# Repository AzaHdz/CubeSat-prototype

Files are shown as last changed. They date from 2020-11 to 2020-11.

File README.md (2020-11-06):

# CubeSat-prototype
Design, Build and test
###### STR: Structure, EPS: Electrical power Subsystem, CDH: Command data and handling, COM: Communications, ADC: Attitude Determination and Control, GCS: Ground Control Station
#### The purpose of this project is to develop the prototype of a CubeSat 1U type satellite, used in real space missions. 
#### 6 subsystems and a Ground control station were designed: EPS, Payload, CDH, COM, ADC, GCS and STR.
#### each subsystem was designed, built and tested
#### Communication protocols used: UART, I2C, Analog, SPI, Zigbee
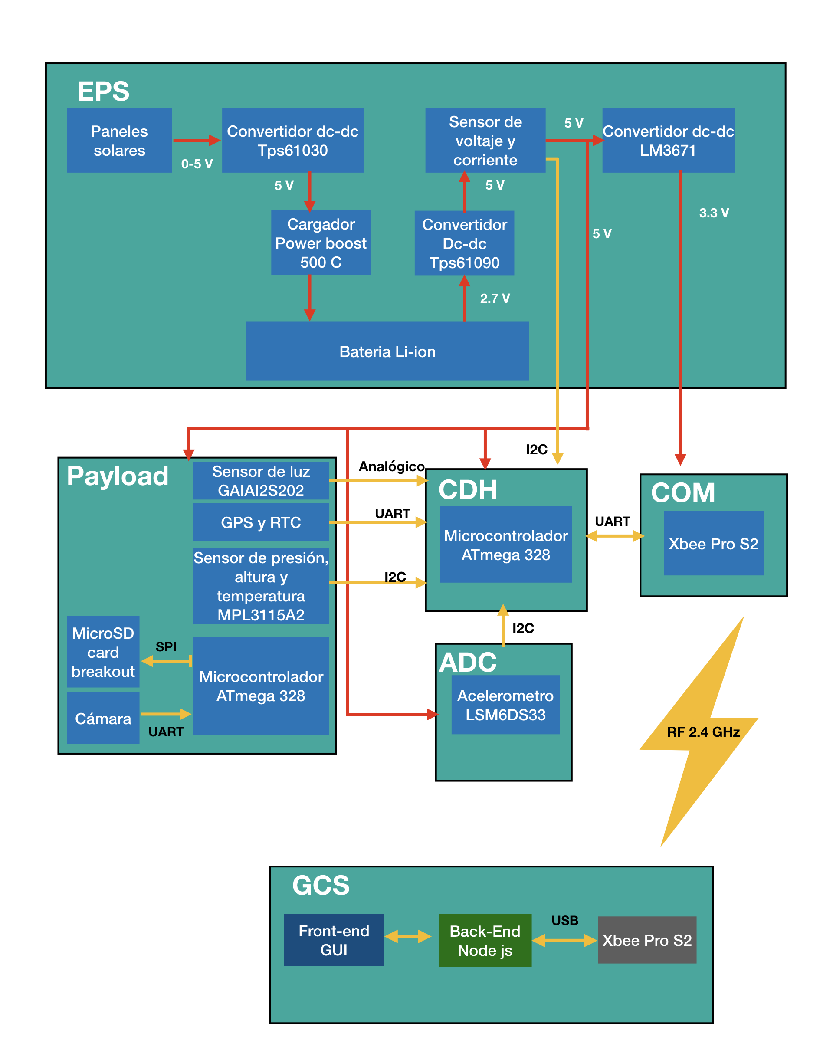
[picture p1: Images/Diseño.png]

#### The STR was designed in fusion 360 and built with  a 3d printer.
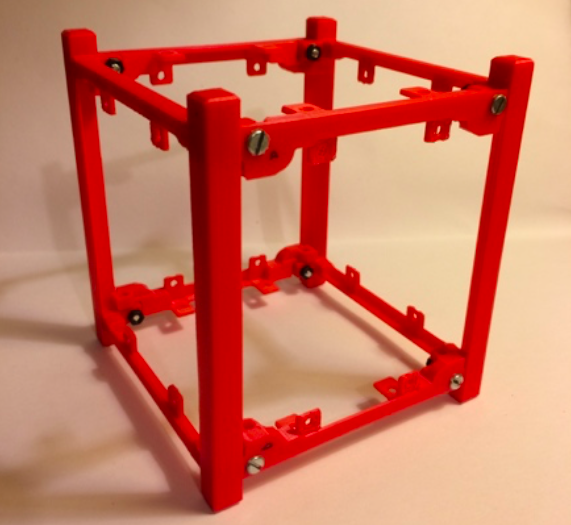
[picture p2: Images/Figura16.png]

#### 5 pcb were designed in eagle and later they were manufactured in a chinese company
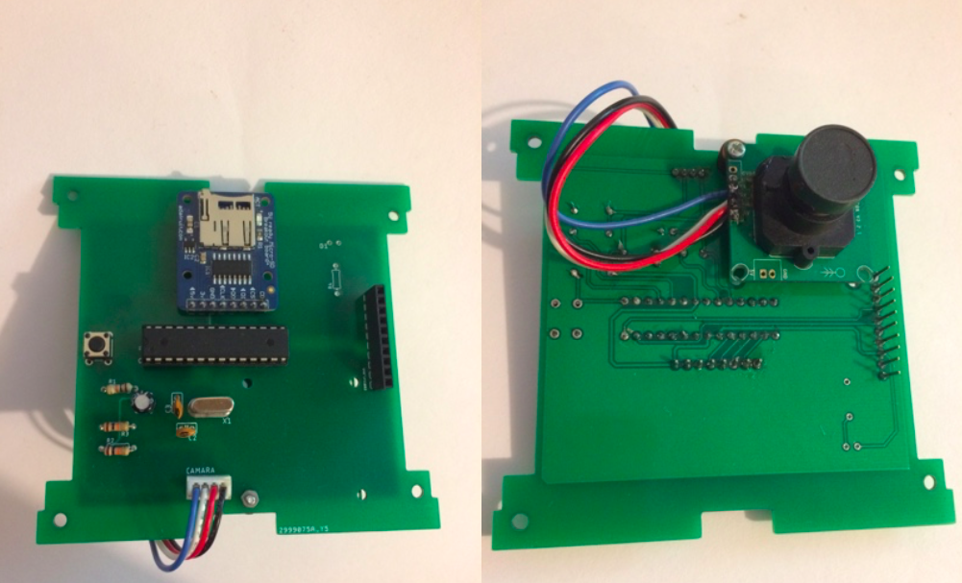
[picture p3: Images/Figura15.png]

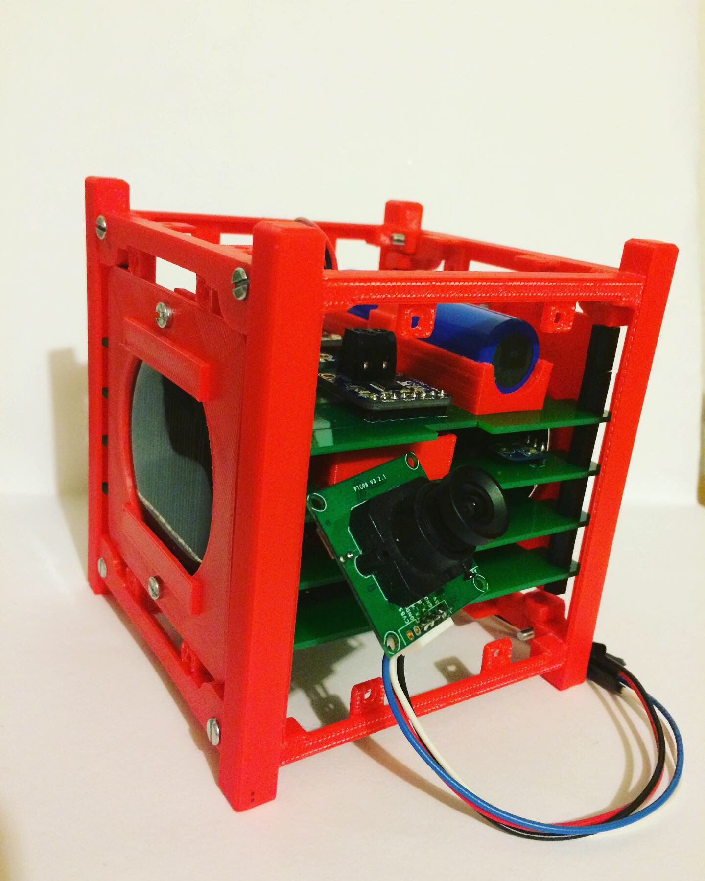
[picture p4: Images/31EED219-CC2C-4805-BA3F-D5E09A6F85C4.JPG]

#### The two microcontrollers were programmed with the Arduino IDE.
#### The GUI was built with Node js and deployed as a web App.
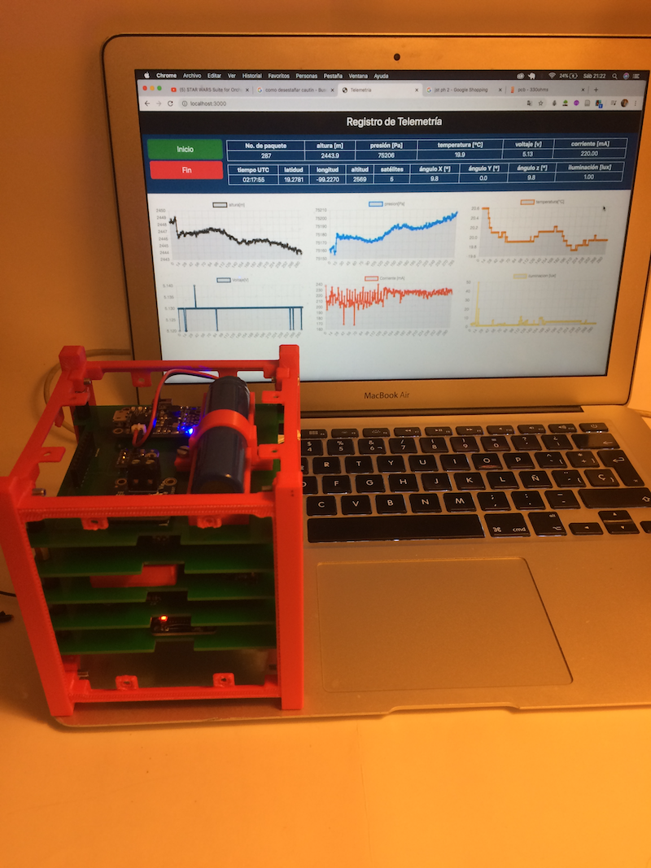
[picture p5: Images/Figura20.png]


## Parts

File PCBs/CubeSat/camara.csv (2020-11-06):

Part | Value | Device | Package | Description | POPULARITY | PROD_ID | SF_SKU | SPICEPREFIX | VALUE
C1 | 10 uF | C-US025-025X050 | C025-025X050 | CAPACITOR, American symbol | 0 |  |  | C
C2 | 22 pF | C-US025-025X050 | C025-025X050 | CAPACITOR, American symbol | 0 |  |  | C
C3 | 22 | C-US025-025X050 | C025-025X050 | CAPACITOR, American symbol | 0 |  |  | C
CAMARA |  | JST-PH4 | JST-PH4
CUBESAT_BUS |  | CONN_10";1X10" | Multi connection point. Often used as Generic Header-pin footprint for 0.1 inch spaced/style header connections |  | CONN-11563
D1 |  | BEAGLEBONE_BLUE_LED-3MM-NO_SILK | BEAGLEBONE_BLUE_BEAGLEBONE_BLUE_LED3MM-NS | LEDs
MEMORIASD |  | CONN_08";1X08" | Multi connection point. Often used as Generic Header-pin footprint for 0.1 inch spaced/style header connections |  | CONN-08438
R1 |  | R-US_0204/7 | 0204/7 | RESISTOR, American symbol | 48 |  |  | 10k
R2 | 10 k | R-US_0204/7 | 0204/7 | RESISTOR, American symbol | 48 |  |  | R
R3 | 10 k | R-US_0204/7 | 0204/7 | RESISTOR, American symbol | 48 |  |  | R
R4 | 330 | R-US_0204/7 | 0204/7 | RESISTOR, American symbol | 48 |  |  | R
S1 | MOMENTARY-SWITCH-SPST-PTH-6.0MM | MOMENTARY-SWITCH-SPST-PTH-6.0MM | TACTILE_SWITCH_PTH_6.0MM | Momentary Switch (Pushbutton) - SPST |  | SWCH-08441 | COM-00097
U1 | 328P | ATMEGA328P_PDIP | DIP28 | Atmel 328P |  | IC-09136 |  |  | 328P
X1 | CRYSTALS-NOGND-HC49 | CRYSTALS-NOGND-HC49 | HC49 | CRYSTALS CAN NOT GROUNDED | 16MHZ

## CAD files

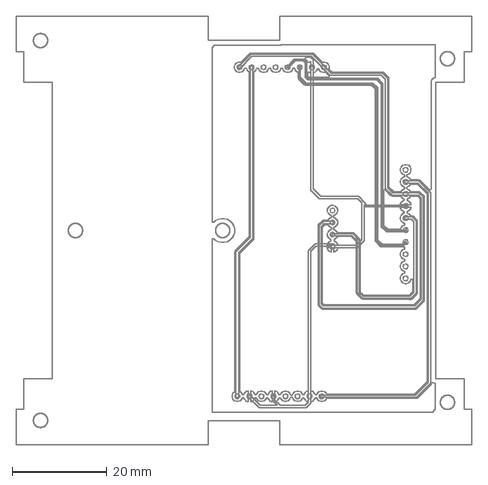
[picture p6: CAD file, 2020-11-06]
PCBs/CubeSat/bateria EPS.dxf
95.9 x 90.2 mm

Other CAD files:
Structure/STR.f3z

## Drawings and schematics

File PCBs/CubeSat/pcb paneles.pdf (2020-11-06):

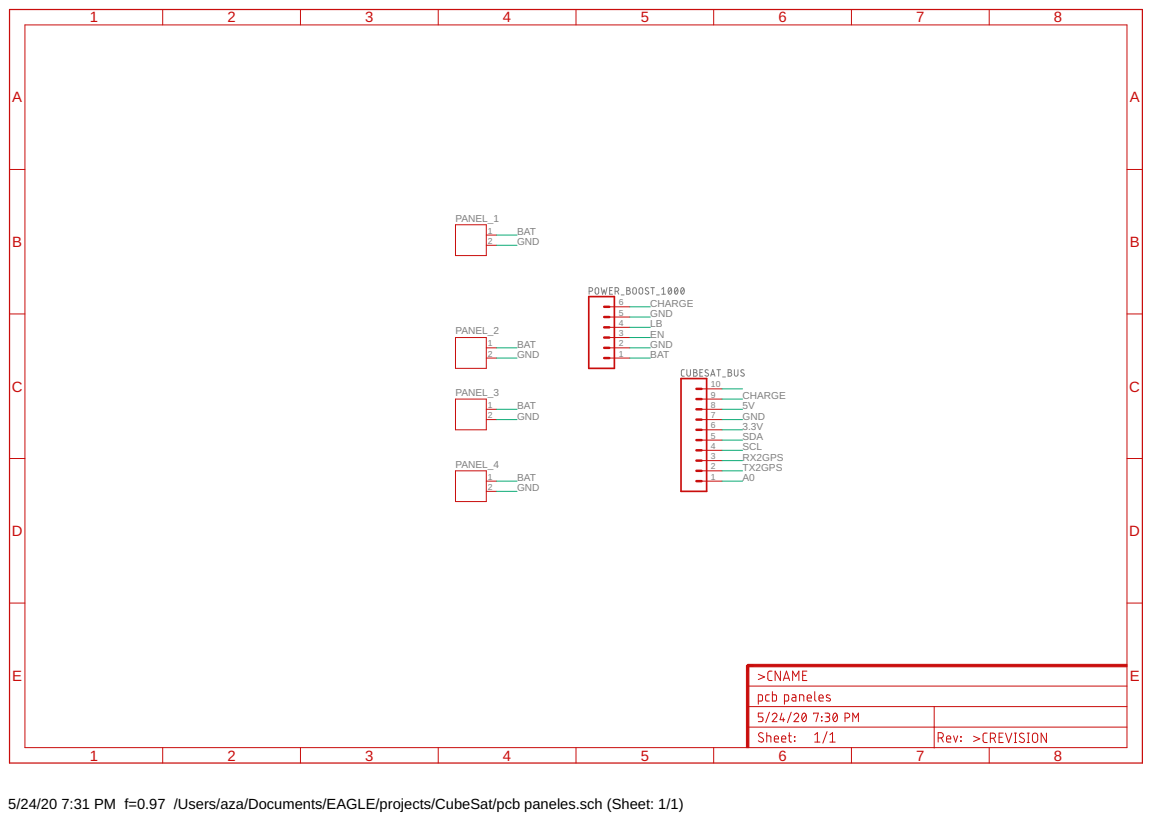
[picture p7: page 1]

5/24/20 7:31 PM f=0.97 /Users/aza/Documents/EAGLE/projects/CubeSat/pcb paneles.sch (Sheet: 1/1)

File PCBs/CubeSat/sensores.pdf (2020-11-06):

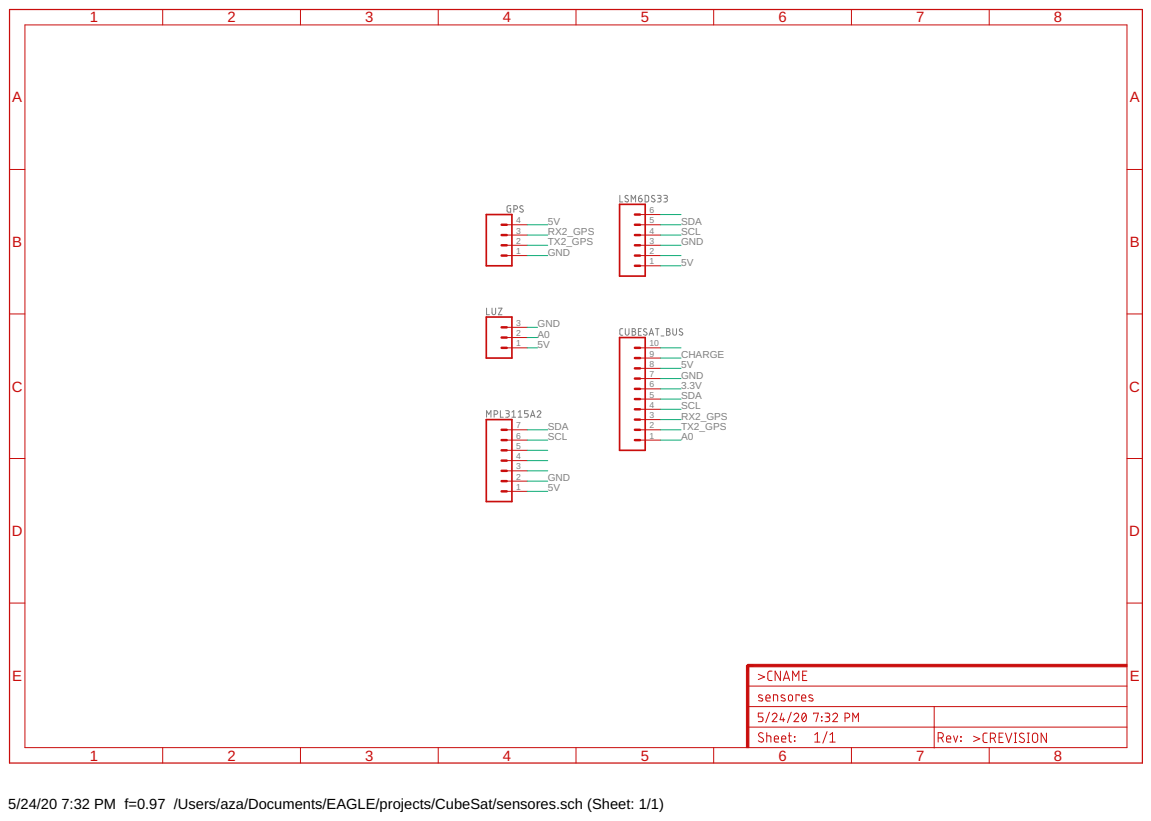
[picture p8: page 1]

5/24/20 7:32 PM f=0.97 /Users/aza/Documents/EAGLE/projects/CubeSat/sensores.sch (Sheet: 1/1)

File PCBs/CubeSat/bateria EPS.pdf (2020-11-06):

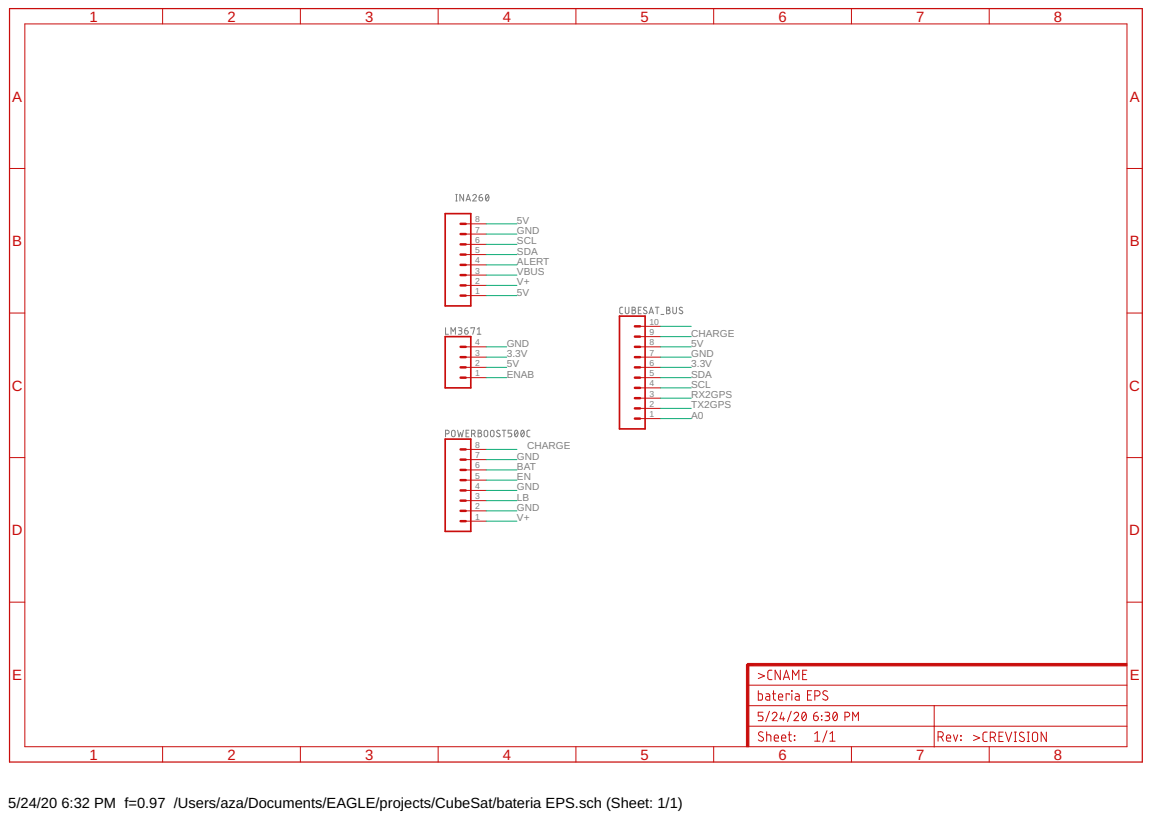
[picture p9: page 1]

5/24/20 6:32 PM f=0.97 /Users/aza/Documents/EAGLE/projects/CubeSat/bateria EPS.sch (Sheet: 1/1)

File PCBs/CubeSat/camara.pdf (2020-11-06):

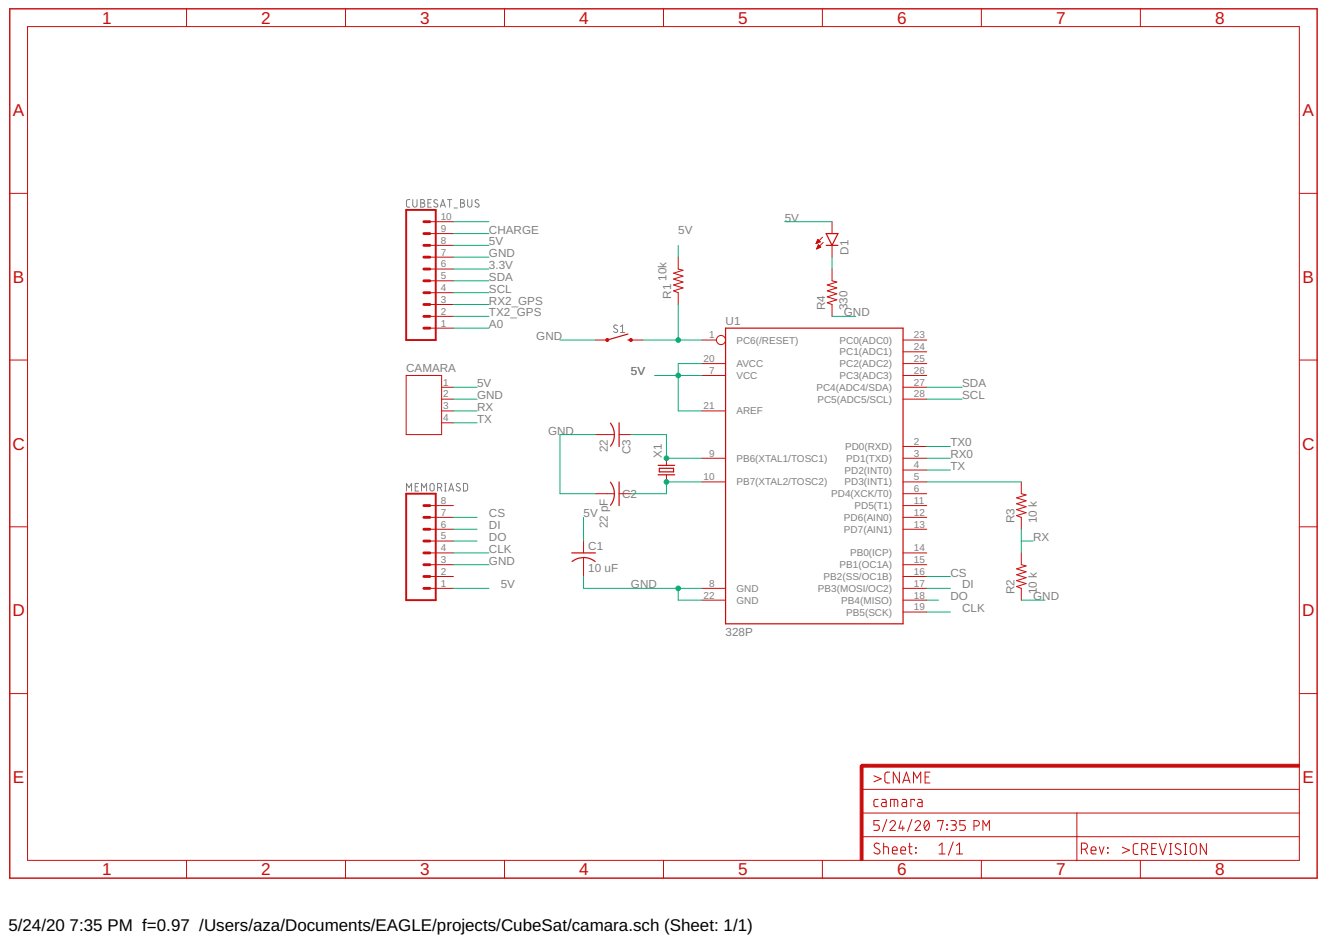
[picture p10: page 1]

5/24/20 7:35 PM f=0.97 /Users/aza/Documents/EAGLE/projects/CubeSat/camara.sch (Sheet: 1/1)

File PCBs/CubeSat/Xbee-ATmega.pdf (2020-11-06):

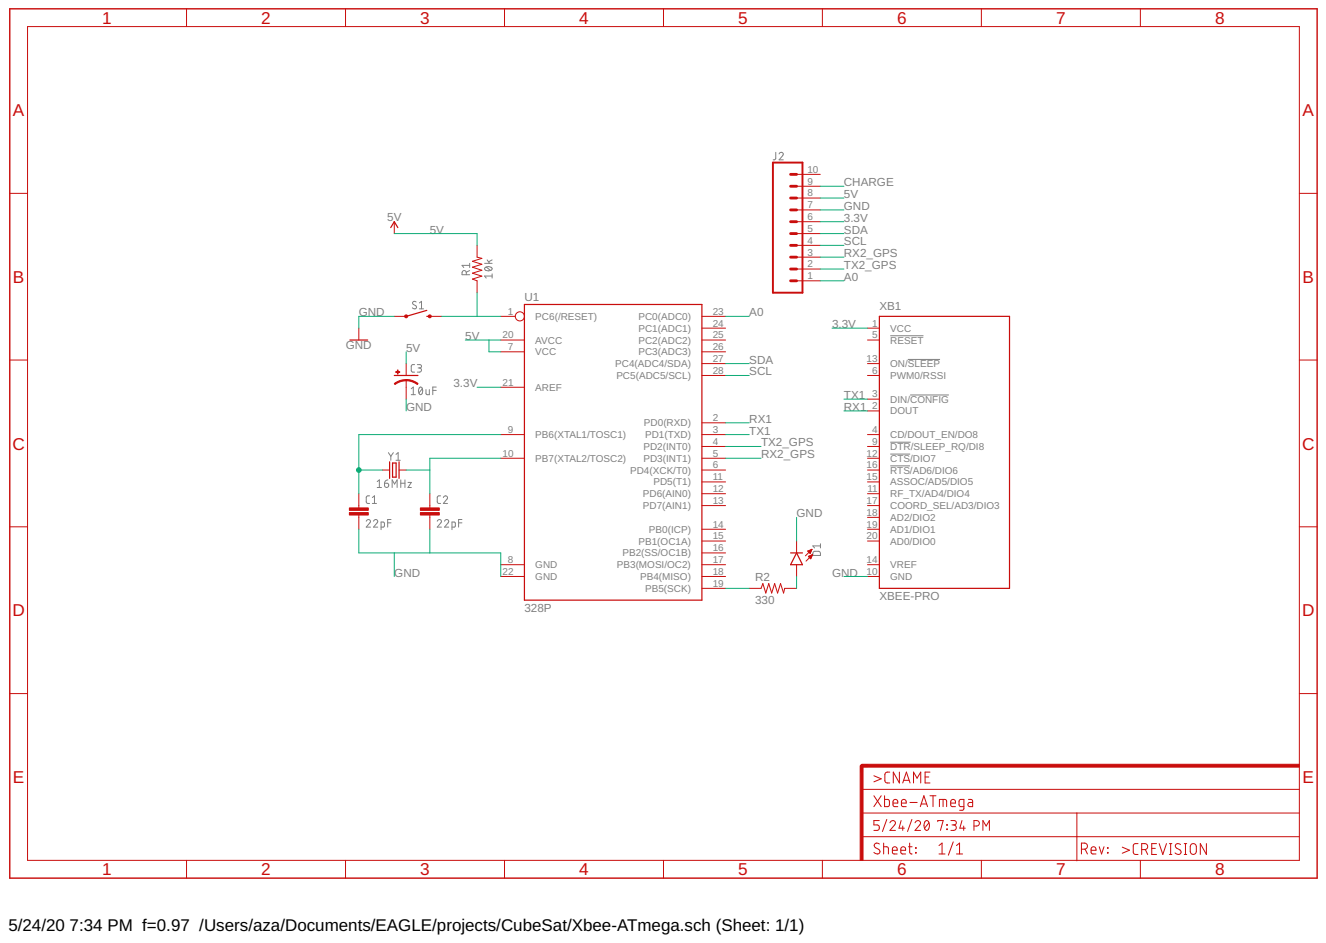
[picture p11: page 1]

5/24/20 7:34 PM f=0.97 /Users/aza/Documents/EAGLE/projects/CubeSat/Xbee-ATmega.sch (Sheet: 1/1)

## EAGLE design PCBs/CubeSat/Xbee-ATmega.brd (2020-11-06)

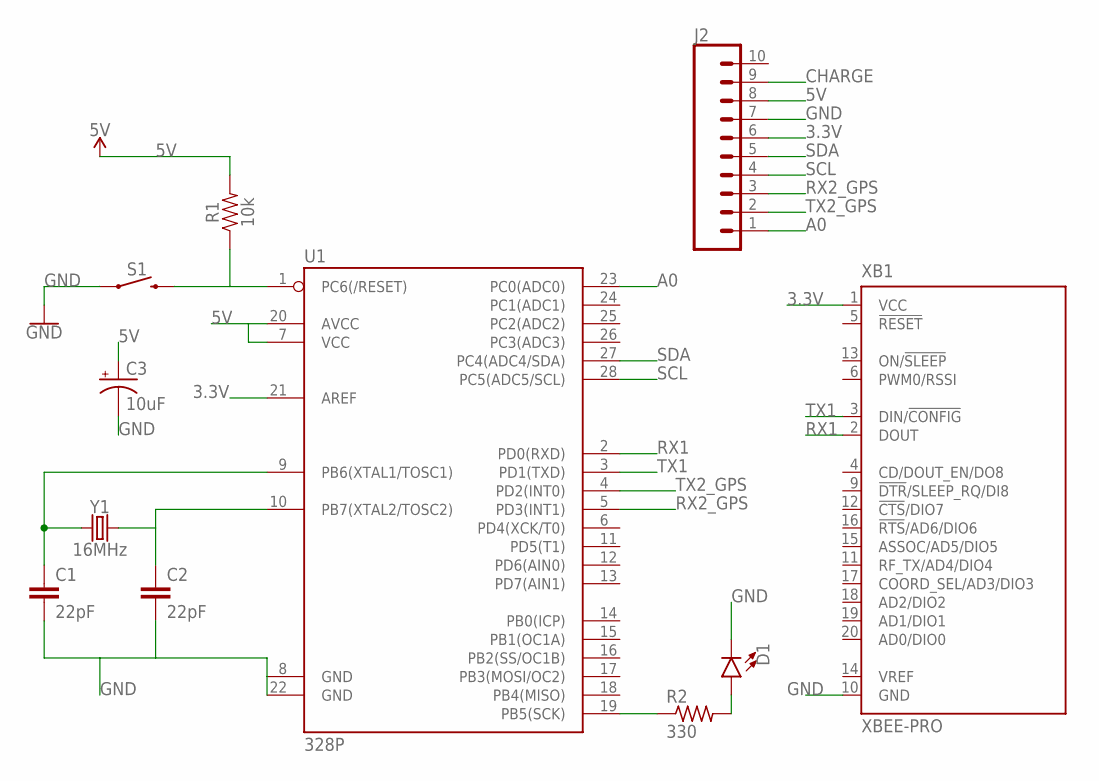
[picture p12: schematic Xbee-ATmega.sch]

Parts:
C1, C2: 22pF; CAP-PTH-2.54
C3: 10uF; CPOL-RADIAL-2.5MM-5MM
D1: LED5MM; LED_5MM
J2: CONN_10"; 1X10
R1: 10k; AXIAL-0.3
R2: 330; 0207/7
S1: MOMENTARY-SWITCH-SPST-PTH-6.0MM; TACTILE_SWITCH_PTH_6.0MM
U1: 328P; DIP28
XB1: XBEE-PRO
Y1: 16MHz; HC49US

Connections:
3.3V: J2.6, U1.21 (AREF), XB1.1 (VCC)
5V: C3.1 (+), J2.8, R1.P$2 (2), U1.7 (VCC), U1.20 (AVCC)
A0: J2.1, U1.23 (PC0(ADC0))
CHARGE: J2.9
GND: C1.2, C2.2, C3.2 (-), D1.K (C), J2.7, S1.1, U1.8 (GND), U1.22 (GND), XB1.10 (GND)
unnamed: R1.P$1 (1), S1.3 (2), U1.1 (PC6(/RESET))
unnamed: C2.1, U1.10 (PB7(XTAL2/TOSC2)), Y1.2
unnamed: C1.1, U1.9 (PB6(XTAL1/TOSC1)), Y1.1
unnamed: R2.1, U1.19 (PB5(SCK))
unnamed: D1.A, R2.2
RX1: U1.2 (PD0(RXD)), XB1.2 (DOUT)
RX2_GPS: J2.3, U1.5 (PD3(INT1))
SCL: J2.4, U1.28 (PC5(ADC5/SCL))
SDA: J2.5, U1.27 (PC4(ADC4/SDA))
TX1: U1.3 (PD1(TXD)), XB1.3 (DIN/!CONFIG)
TX2_GPS: J2.2, U1.4 (PD2(INT0))

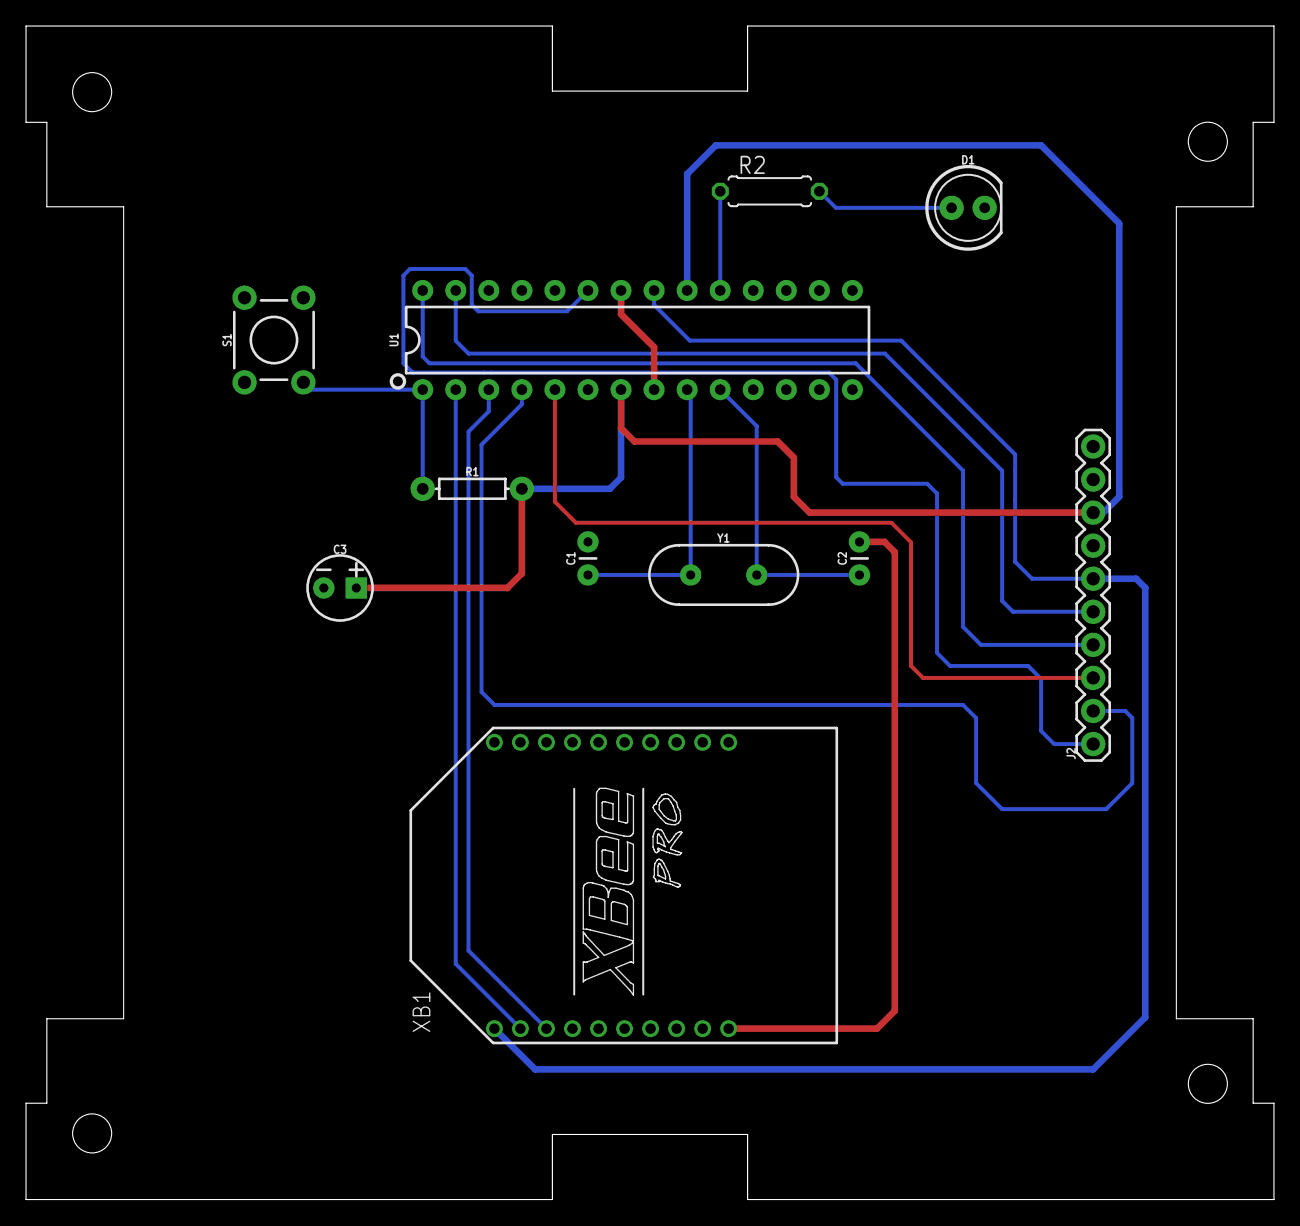
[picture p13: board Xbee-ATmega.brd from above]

Board: 2 copper layers, 95.9 x 90.2 mm, 11 parts (0 on the bottom side), 15 nets.

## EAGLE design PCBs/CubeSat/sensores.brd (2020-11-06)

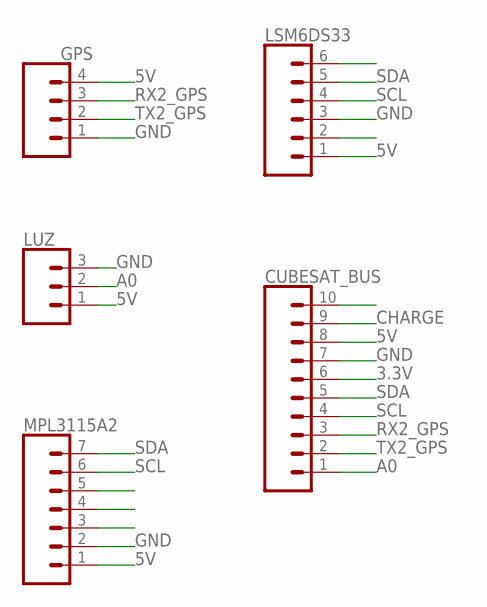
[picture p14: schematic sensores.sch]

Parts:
CUBESAT_BUS: CONN_10"; 1X10
GPS: CONN_04; 1X04
LSM6DS33: CONN_06SILK_FEMALE_PTH; 1X06
LUZ: CONN_03; 1X03
MPL3115A2: CONN_07; 1X07

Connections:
3.3V: CUBESAT_BUS.6
5V: CUBESAT_BUS.8, GPS.4, LSM6DS33.1, LUZ.1, MPL3115A2.1
A0: CUBESAT_BUS.1, LUZ.2
CHARGE: CUBESAT_BUS.9
GND: CUBESAT_BUS.7, GPS.1, LSM6DS33.3, LUZ.3, MPL3115A2.2
RX2_GPS: CUBESAT_BUS.3, GPS.3
SCL: CUBESAT_BUS.4, LSM6DS33.4, MPL3115A2.6
SDA: CUBESAT_BUS.5, LSM6DS33.5, MPL3115A2.7
TX2_GPS: CUBESAT_BUS.2, GPS.2

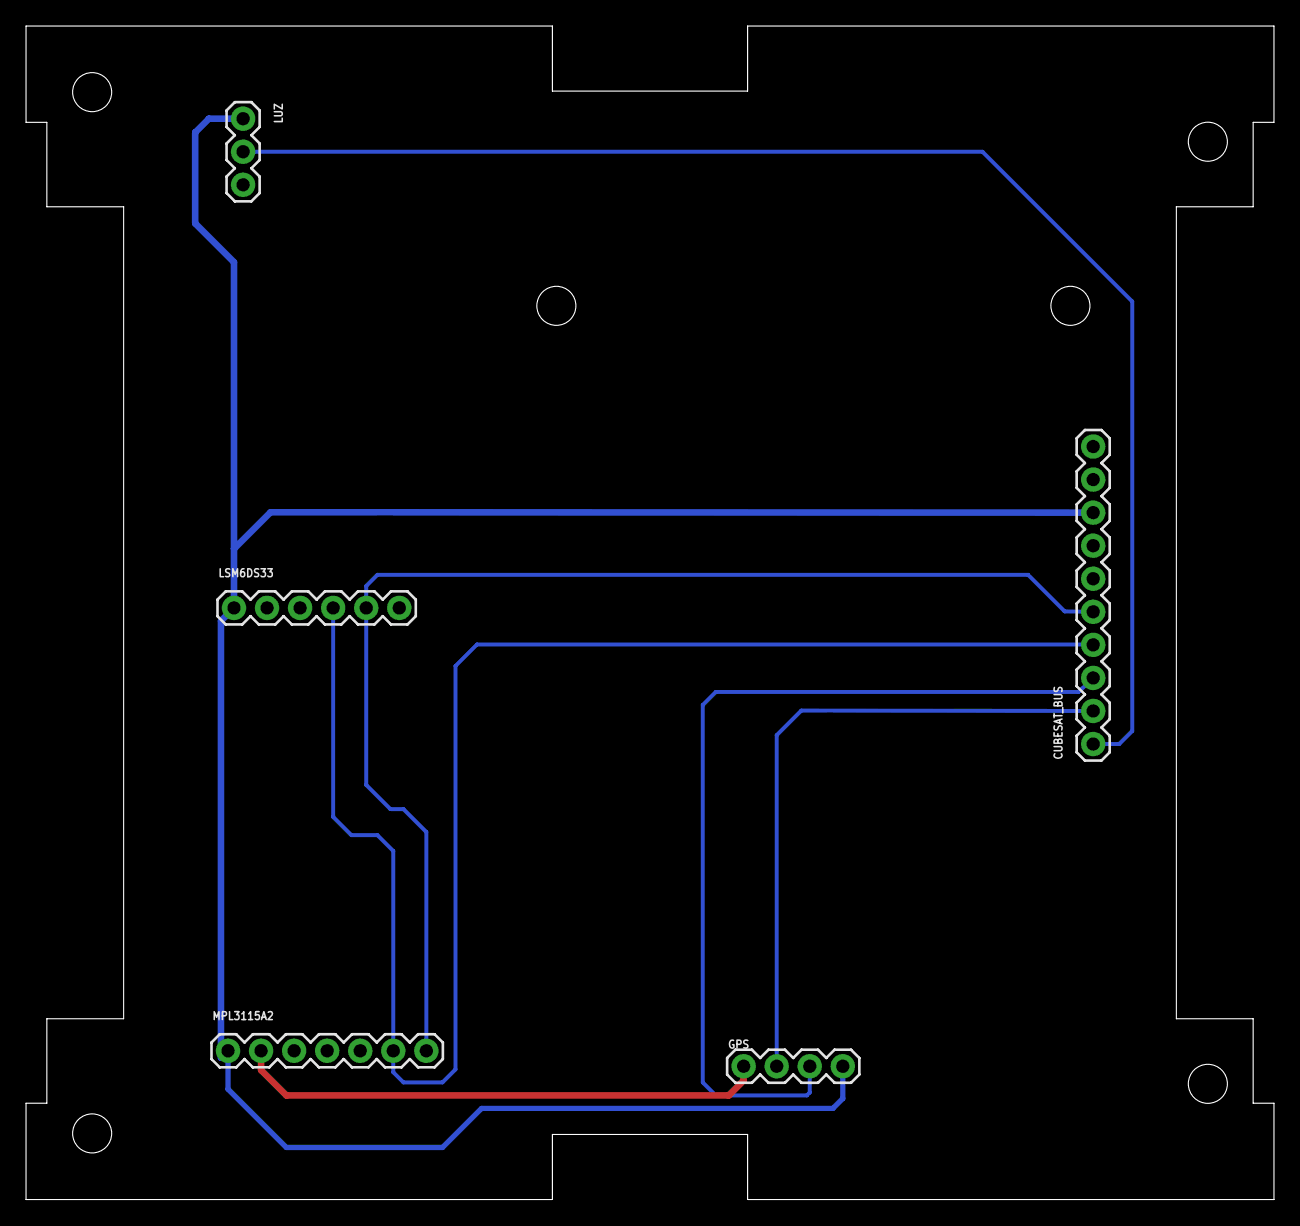
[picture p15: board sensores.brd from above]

Board: 2 copper layers, 95.9 x 90.2 mm, 5 parts (0 on the bottom side), 7 nets.

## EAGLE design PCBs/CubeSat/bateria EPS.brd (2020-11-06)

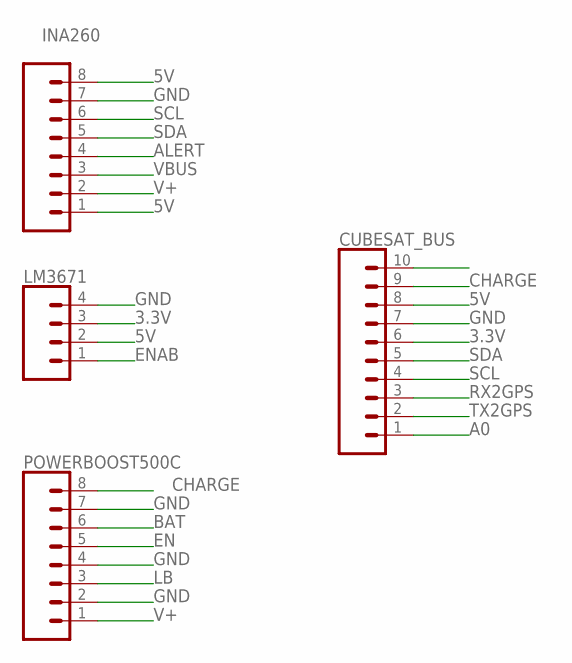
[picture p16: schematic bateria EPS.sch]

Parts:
CUBESAT_BUS: CONN_10"; 1X10
INA260: CONN_08"; 1X08
LM3671: CONN_04PTH; 1X04
POWERBOOST500C: CONN_08"; 1X08

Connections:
3.3V: CUBESAT_BUS.6, LM3671.3
5V: CUBESAT_BUS.8, INA260.1, INA260.8, LM3671.2
A0: CUBESAT_BUS.1
ALERT: INA260.4
BAT: POWERBOOST500C.6
CHARGE: CUBESAT_BUS.9, POWERBOOST500C.8
EN: POWERBOOST500C.5
ENAB: LM3671.1
GND: CUBESAT_BUS.7, INA260.7, LM3671.4, POWERBOOST500C.2, POWERBOOST500C.4, POWERBOOST500C.7
LB: POWERBOOST500C.3
RX2GPS: CUBESAT_BUS.3
SCL: CUBESAT_BUS.4, INA260.6
SDA: CUBESAT_BUS.5, INA260.5
TX2GPS: CUBESAT_BUS.2
V+: INA260.2, POWERBOOST500C.1
VBUS: INA260.3

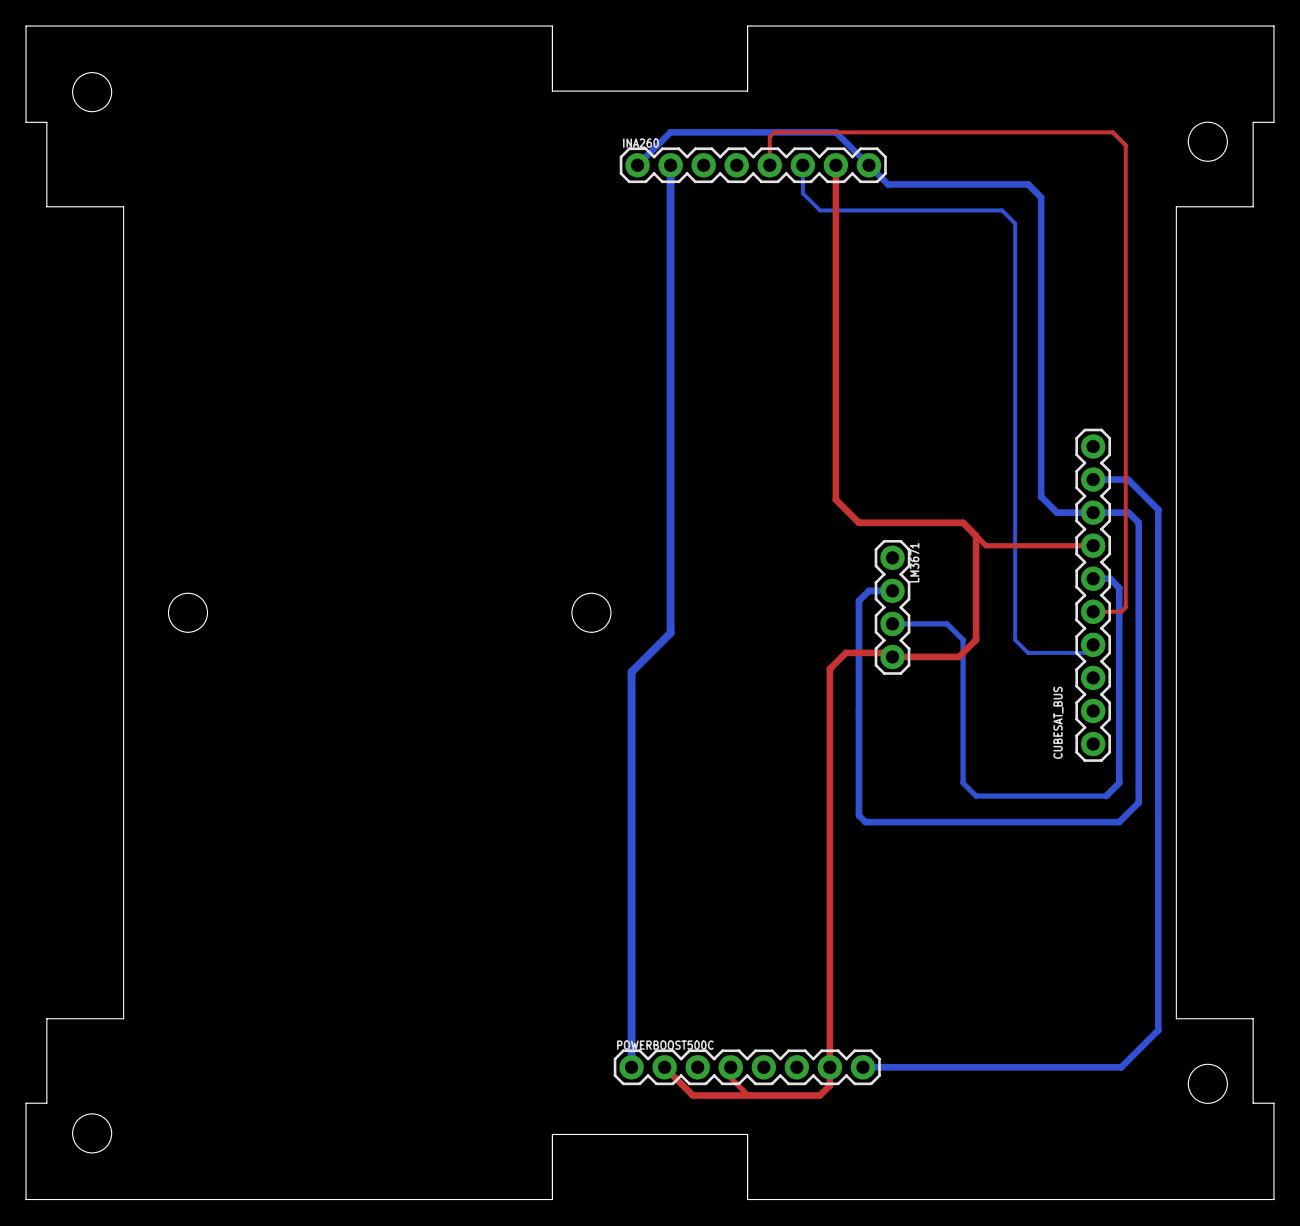
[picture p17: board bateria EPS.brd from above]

Board: 2 copper layers, 95.9 x 90.2 mm, 4 parts (0 on the bottom side), 7 nets.

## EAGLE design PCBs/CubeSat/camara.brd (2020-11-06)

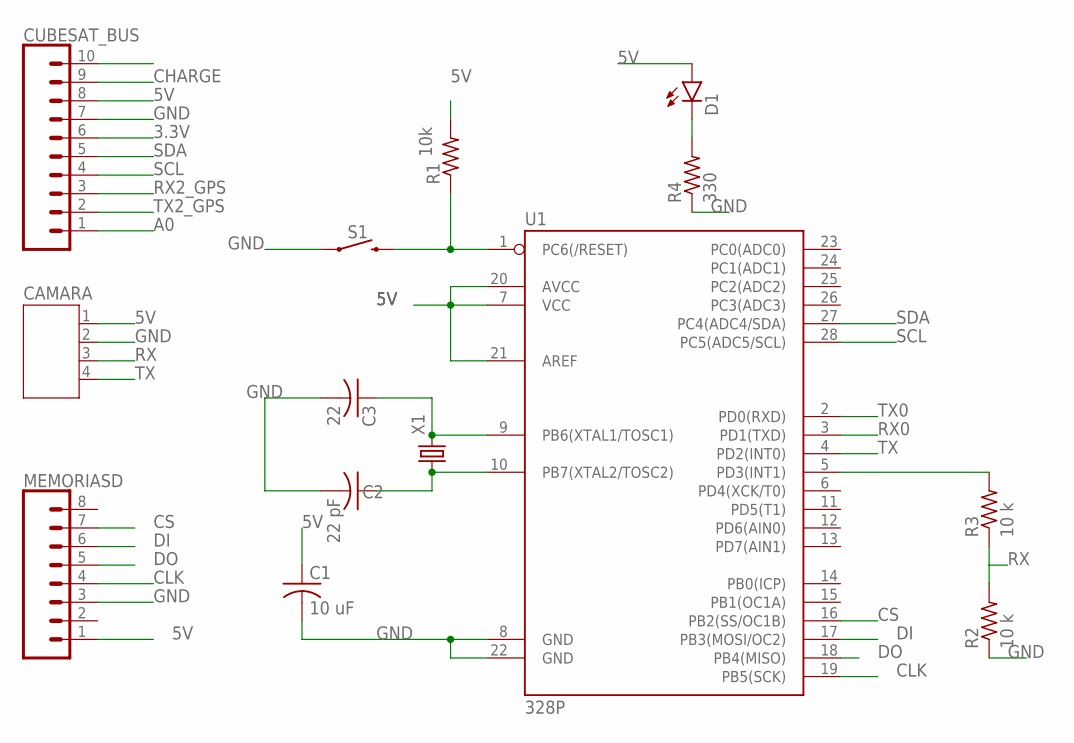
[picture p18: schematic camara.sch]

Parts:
C1: 10 uF; C025-025X050
C2: 22 pF; C025-025X050
C3: 22; C025-025X050
CAMARA: JST-PH4
CUBESAT_BUS: CONN_10"; 1X10
D1: BEAGLEBONE_BLUE_LED-3MM-NO_SILK; BEAGLEBONE_BLUE_BEAGLEBONE_BLUE_LED3MM-NS
MEMORIASD: CONN_08"; 1X08
R1: R-US_0204/7; 0204/7
R2, R3: 10 k; 0204/7
R4: 330; 0204/7
S1: MOMENTARY-SWITCH-SPST-PTH-6.0MM; TACTILE_SWITCH_PTH_6.0MM
U1: 328P; DIP28
X1: CRYSTALS-NOGND-HC49; HC49

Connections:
3.3V: CUBESAT_BUS.6
5V: C1.1, CAMARA.1, CUBESAT_BUS.8, D1.A, MEMORIASD.1, R1.2, U1.7 (VCC), U1.20 (AVCC), U1.21 (AREF)
A0: CUBESAT_BUS.1
CHARGE: CUBESAT_BUS.9
CLK: MEMORIASD.4, U1.19 (PB5(SCK))
CS: MEMORIASD.7, U1.16 (PB2(SS/OC1B))
DI: MEMORIASD.6, U1.17 (PB3(MOSI/OC2))
DO: MEMORIASD.5, U1.18 (PB4(MISO))
GND: C1.2, C2.2, C3.2, CAMARA.2, CUBESAT_BUS.7, MEMORIASD.3, R2.1, R4.1, S1.1, U1.8 (GND), U1.22 (GND)
unnamed: R1.1, S1.3 (2), U1.1 (PC6(/RESET))
unnamed: C3.1, U1.9 (PB6(XTAL1/TOSC1)), X1.2
unnamed: C2.1, U1.10 (PB7(XTAL2/TOSC2)), X1.1
unnamed: R3.2, U1.5 (PD3(INT1))
unnamed: D1.K (C), R4.2
RX: CAMARA.3, R2.2, R3.1
RX0: U1.3 (PD1(TXD))
RX2_GPS: CUBESAT_BUS.3
SCL: CUBESAT_BUS.4, U1.28 (PC5(ADC5/SCL))
SDA: CUBESAT_BUS.5, U1.27 (PC4(ADC4/SDA))
TX: CAMARA.4, U1.4 (PD2(INT0))
TX0: U1.2 (PD0(RXD))
TX2_GPS: CUBESAT_BUS.2

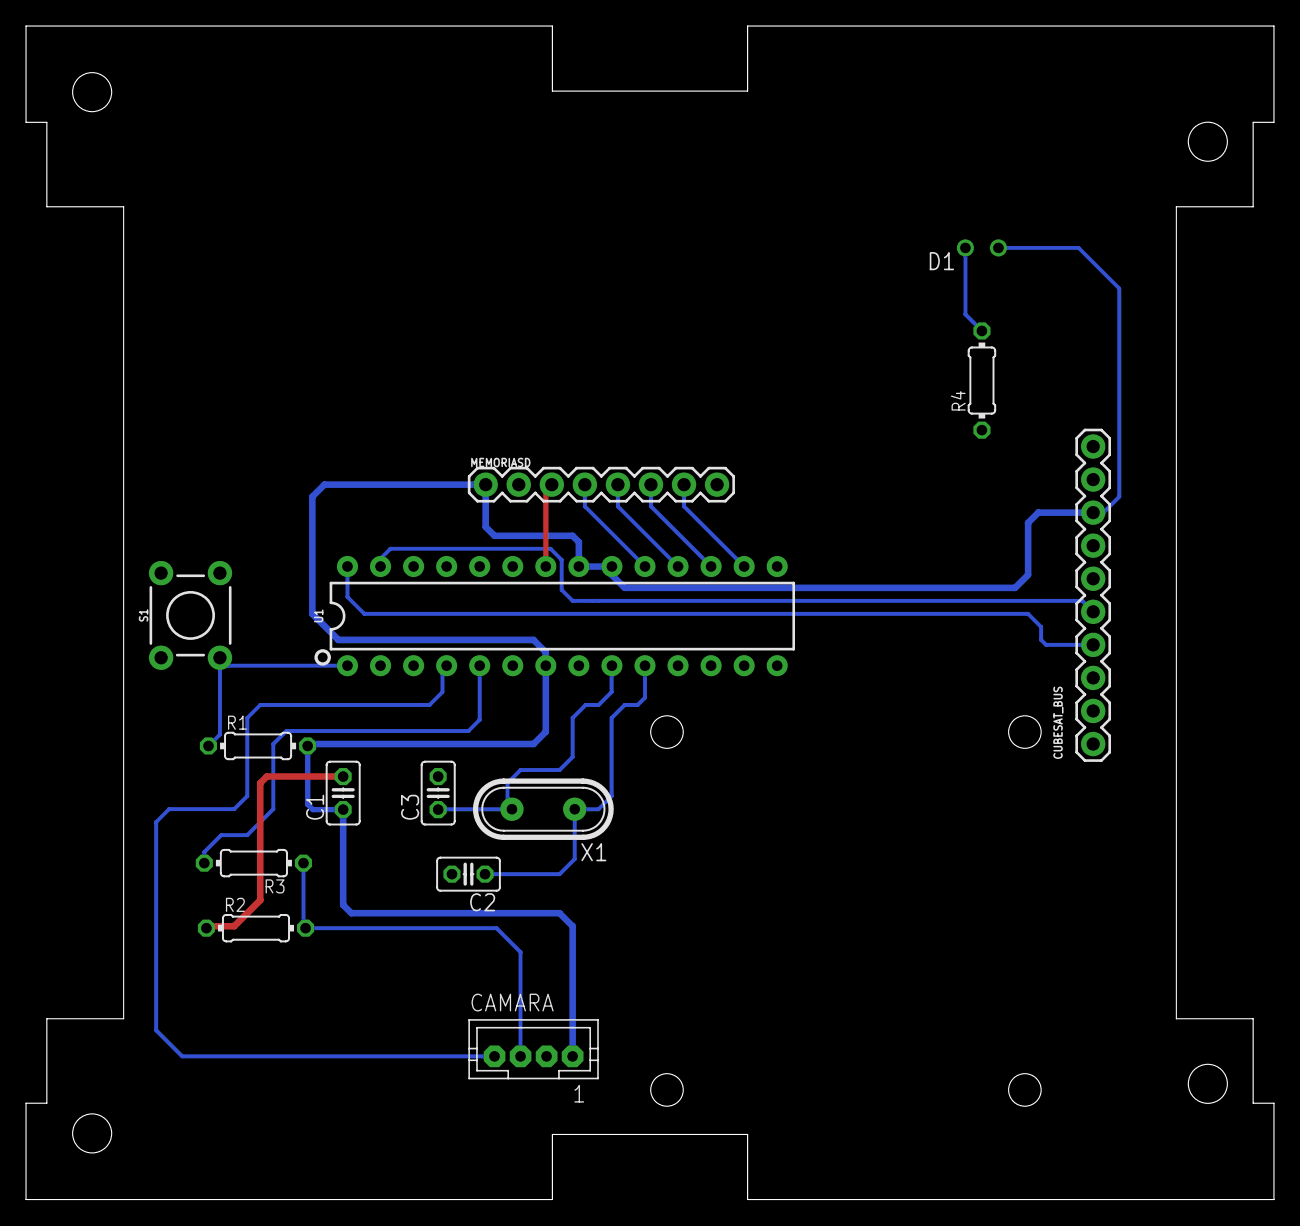
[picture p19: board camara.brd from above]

Board: 2 copper layers, 95.9 x 90.2 mm, 14 parts (0 on the bottom side), 15 nets.

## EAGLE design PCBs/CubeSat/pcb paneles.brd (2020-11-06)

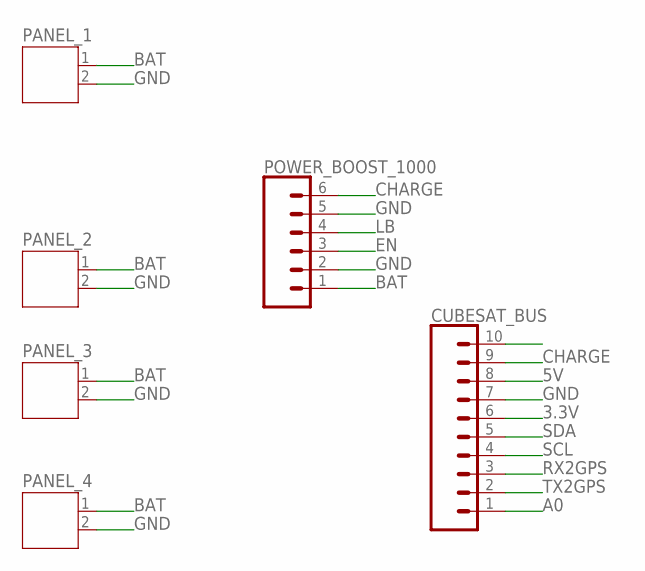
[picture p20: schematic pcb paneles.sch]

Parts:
CUBESAT_BUS: CONN_10"; 1X10
PANEL_1, PANEL_2, PANEL_3, PANEL_4: JST-PH2
POWER_BOOST_1000: CONN_06SILK_FEMALE_PTH; 1X06

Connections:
3.3V: CUBESAT_BUS.6
5V: CUBESAT_BUS.8
A0: CUBESAT_BUS.1
BAT: PANEL_1.1, PANEL_2.1, PANEL_3.1, PANEL_4.1, POWER_BOOST_1000.1
CHARGE: CUBESAT_BUS.9, POWER_BOOST_1000.6
EN: POWER_BOOST_1000.3
GND: CUBESAT_BUS.7, PANEL_1.2, PANEL_2.2, PANEL_3.2, PANEL_4.2, POWER_BOOST_1000.2, POWER_BOOST_1000.5
LB: POWER_BOOST_1000.4
RX2GPS: CUBESAT_BUS.3
SCL: CUBESAT_BUS.4
SDA: CUBESAT_BUS.5
TX2GPS: CUBESAT_BUS.2

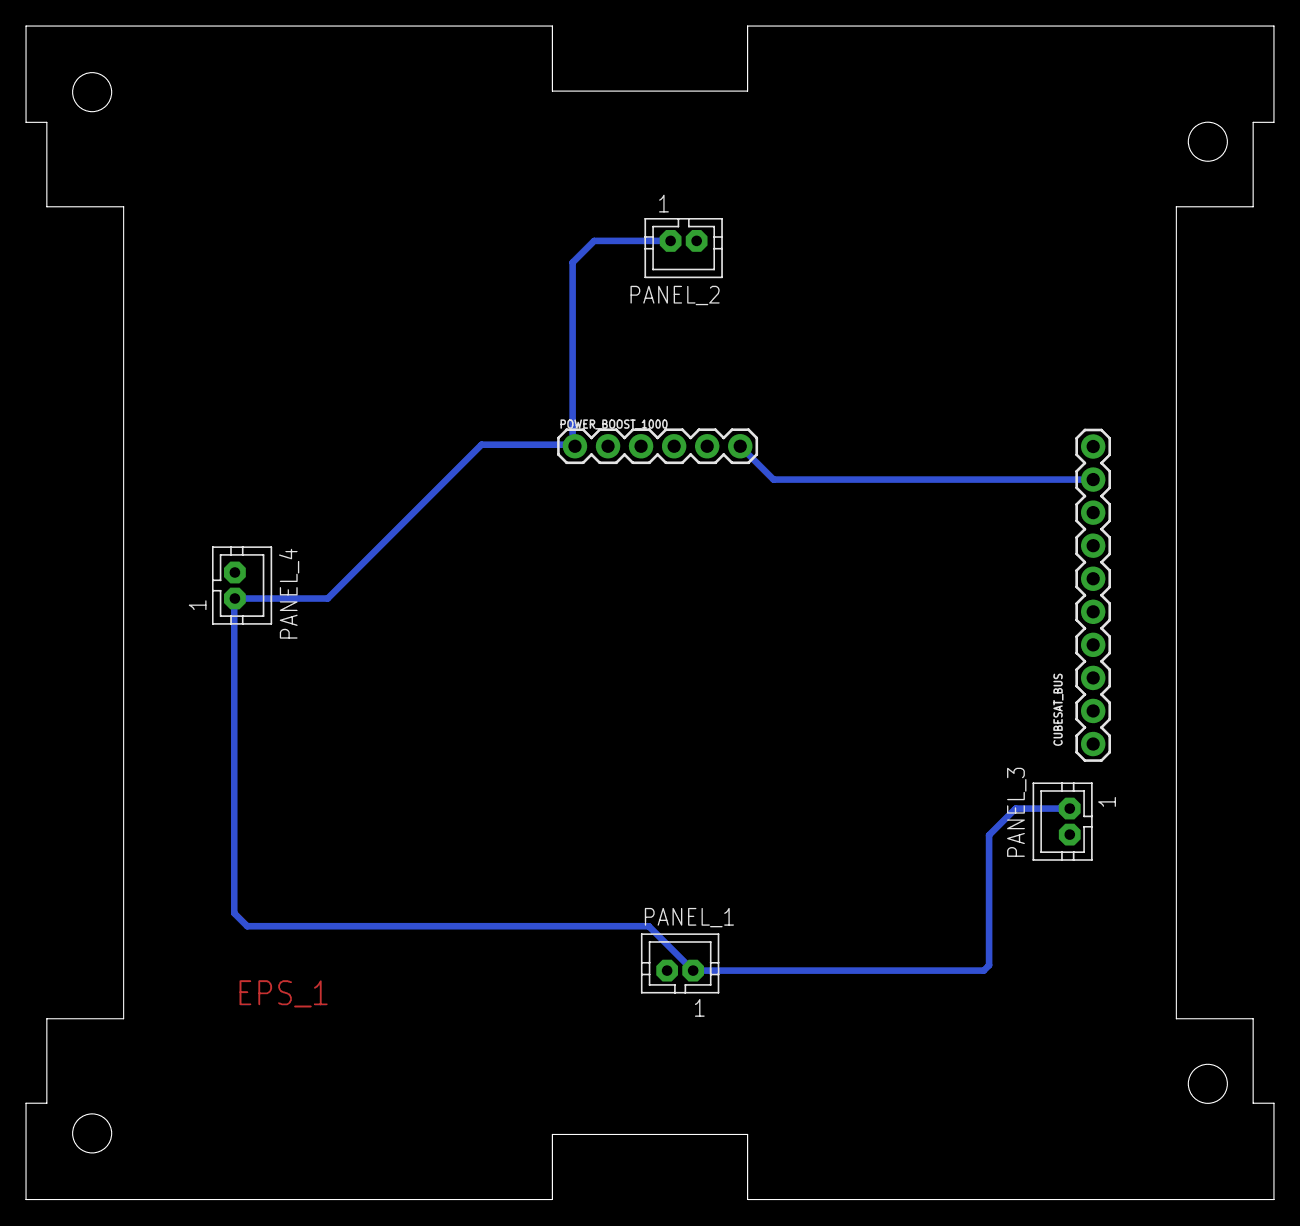
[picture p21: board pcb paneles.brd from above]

Board: 2 copper layers, 95.9 x 90.2 mm, 6 parts (0 on the bottom side), 3 nets.

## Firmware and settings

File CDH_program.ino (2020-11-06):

#include <TinyGPS++.h>
#include <SoftwareSerial.h>
#include <Wire.h>
#include <Adafruit_MPL3115A2.h>
#include <Adafruit_INA260.h>
#include <Adafruit_LSM6DS33.h>
int comando;
int estado = 0;
int count = 1;
int RXPin = 2;
int TXPin = 3;
int GPSBaud = 9600;
float latitud, longitud;
int satelites, altitud, hora, minuto, segundo;
//int senVol = A1; // pin del sensor analogico de voltaje
// Create a TinyGPS++ object
TinyGPSPlus gps;
// Create a software serial port called "gpsSerial"
SoftwareSerial gpsSerial(RXPin, TXPin);
//sensor de luz
int sensor_luz_pin = A0;
float rango_de_lectura = 1024;//3.3
float vr = 3.3;
//mpl presion altura temperatura
Adafruit_MPL3115A2 baro = Adafruit_MPL3115A2();
//Sensor de voltaje y corriente INA
Adafruit_INA260 ina260 = Adafruit_INA260();
float voltaje,corriente;
//IMU
const float g = 9.78, pi =3.14; //g en la CDMX
float acx = 0,
      acy = 0,
      acz = 0,
      tiltx = 0,
      tilty = 0,
      tiltz = 0;
Adafruit_LSM6DS33 lsm6ds33; 
void setup() {
  analogReference(EXTERNAL);
  Serial.begin(115200);
  gpsSerial.begin(GPSBaud);
  //Sensor de voltaje INA
  while (!Serial) { delay(10); }

  //Serial.println("Adafruit INA260 Test");

  if (!ina260.begin()) {
    Serial.println("Couldn't find INA260 chip");
    while (1);
  }
  //Serial.println("Found INA260 chip");
//IMU
 //Serial.println("Adafruit LSM6DS33 test!");

  if (!lsm6ds33.begin_I2C()) {
    // if (!lsm6ds33.begin_SPI(LSM_CS)) {
    // if (!lsm6ds33.begin_SPI(LSM_CS, LSM_SCK, LSM_MISO, LSM_MOSI)) {
    Serial.println("Failed to find LSM6DS33 chip");
    while (1) {
      delay(10);
    }
  }
  //Serial.println("LSM6DS33 Found!");

  lsm6ds33.configInt1(false, false, true); // accelerometer DRDY on INT1
  lsm6ds33.configInt2(false, true, false); // gyro DRDY on INT2// put your setup code here, to run once:
}
void loop() {
  //revisa el comando
   if(Serial.available()>0){
    comando = Serial.read();
    if(comando == 'Y'){
      estado = 1;
      } else {
      estado = 0;
      }
   }
   if (estado == 1){
     if (! baro.begin()) 
    {
      Serial.println("Couldnt find sensor");
      return;
     }
  while (gpsSerial.available() > 0)
      if (gps.encode(gpsSerial.read()))
        gpsInfo();   
  float pascals = baro.getPressure();
  float altmTemporal = baro.getAltitude();
  float tempC = baro.getTemperature();
  float valorDeCalibracion;
  if (count == 130){
     valorDeCalibracion = altmTemporal;
    }
  //float voltaje = (float)25*analogRead(senVol)/1023;
  int valor = analogRead(sensor_luz_pin);
  //sonsor de voltaje INA
  voltaje = ina260.readBusVoltage()/1000;
  corriente = ina260.readCurrent();
  //imu
  sensors_event_t accel;
  sensors_event_t gyro;
  sensors_event_t temp;
  lsm6ds33.getEvent(&accel, &gyro, &temp);
  acx = accel.acceleration.x / g; // valor en g
  acy = accel.acceleration.y / g;
  acz = accel.acceleration.z / g;
  // put your main code here, to run repeatedly:
  tiltx = atan(acx/(sqrt(pow(acy,2)+pow(acz,2))))*(180/pi);
  tilty = atan(acy/(sqrt(pow(acx,2)+pow(acz,2))))*(180/pi);
  tiltz = atan((sqrt(pow(acx,2)+pow(acy,2)))/acz)*(180/pi);
      //Se imprimen los valores 
      Serial.print(count);  Serial.print(',');
      if(count > 130){ //solo ese enviará hasta que el valor este calibrado
        Serial.print(altmTemporal - valorDeCalibracion, 1); Serial.print(',');
       } else {Serial.print(0); Serial.print(',');}
      Serial.print(pascals, 0); Serial.print(',');
      Serial.print(tempC, 1); Serial.print(',');
      Serial.print(voltaje); Serial.print(',');//voltaje
      delay(15);  
      Serial.print(corriente); Serial.print(',');
      delay(15);
      if (hora < 10) Serial.print(F("0")); 
      Serial.print(hora); Serial.print(":");
      if (minuto < 10) Serial.print(F("0"));
      Serial.print(minuto); Serial.print(":");
      if (segundo < 10) Serial.print(F("0"));
      Serial.print(segundo); Serial.print(','); 
      delay(15);  
      Serial.print(latitud, 5); Serial.print(',');
      delay(15);
      Serial.print(longitud, 5); Serial.print(',');
      delay(15);
      Serial.print(altitud, 1); Serial.print(',');
      delay(15);
      Serial.print(satelites); Serial.print(',');
      delay(15);
      Serial.print(tiltx, 1); Serial.print(',');
      Serial.print(tilty, 1); Serial.print(',');
      Serial.print(tiltz, 1); Serial.print(',');
      delay(15);  
      Serial.println(valorALux(valor)); 
  count ++;
  delay(500);
   }
}
 void gpsInfo(){
     if (gps.location.isValid())
          { 
            latitud = gps.location.lat();      
            longitud = gps.location.lng();
          } else {
            latitud = 0;
            longitud = 0;
            }
     if (gps.altitude.isValid())
           {
            altitud = gps.altitude.meters(); 
           } else{
            altitud = 0;
            }
     if (gps.time.isValid())
          {
            hora = gps.time.hour();
            minuto = gps.time.minute();
            segundo = gps.time.second();
           } else {
            hora = 0;
            minuto = 0;
            segundo = 0;
            }             
     if (gps.satellites.isValid())
          {
           satelites = gps.satellites.value();    
            } else {
              satelites = 0; 
              }
     }
float valorALux(int valorAn)
{
  float v = valorAn*vr/rango_de_lectura; //se obtiene el voltaje de salida del sensor
  float io=(v/68000)*1000000;// se obtiene la corriente de salida del sensro por ley de ohm en uA
  //se despeja I=10log(ev) [uA]; --> ev=10^(I/10) 
   return pow(10, io/10);// ev
  }

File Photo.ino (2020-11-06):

#include <Adafruit_VC0706.h>
#include <SPI.h>
#include <SD.h>

// comment out this line if using Arduino V23 or earlier
#include <SoftwareSerial.h>         


#define chipSelect 10

// Using SoftwareSerial (Arduino 1.0+) or NewSoftSerial (Arduino 0023 & prior):
#if ARDUINO >= 100
// On Uno: camera TX connected to pin 2, camera RX to pin 3:
SoftwareSerial cameraconnection = SoftwareSerial(2, 3);
// On Mega: camera TX connected to pin 69 (A15), camera RX to pin 3:
//SoftwareSerial cameraconnection = SoftwareSerial(69, 3);
#else
NewSoftSerial cameraconnection = NewSoftSerial(2, 3);
#endif

Adafruit_VC0706 cam = Adafruit_VC0706(&cameraconnection);

void setup() {

#if !defined(SOFTWARE_SPI)
#if defined(__AVR_ATmega1280__) || defined(__AVR_ATmega2560__)
  if(chipSelect != 53) pinMode(53, OUTPUT); // SS on Mega
#else
  if(chipSelect != 10) pinMode(10, OUTPUT); // SS on Uno, etc.
#endif
#endif

  Serial.begin(9600);
  
  Serial.println("VC0706 Camera snapshot test");
  
  // see if the card is present and can be initialized:
  if (!SD.begin(chipSelect)) {
    Serial.println("Card failed, or not present");
    // don't do anything more:
    return;
  }  
  
  // Try to locate the camera
  if (cam.begin()) {
    Serial.println("Camera Found:");
  } else {
    Serial.println("No camera found?");
    return;
  }
  // Print out the camera version information (optional)
  char *reply = cam.getVersion();
  if (reply == 0) {
    Serial.print("Failed to get version");
  } else {
    Serial.println("-----------------");
    Serial.print(reply);
    Serial.println("-----------------");
  }

  // Set the picture size - you can choose one of 640x480, 320x240 or 160x120 
  // Remember that bigger pictures take longer to transmit!
  
  cam.setImageSize(VC0706_640x480);        // biggest
  //cam.setImageSize(VC0706_320x240);        // medium
  //cam.setImageSize(VC0706_160x120);          // small

  // You can read the size back from the camera (optional, but maybe useful?)
  uint8_t imgsize = cam.getImageSize();
  Serial.print("Image size: ");
  if (imgsize == VC0706_640x480) Serial.println("640x480");
  if (imgsize == VC0706_320x240) Serial.println("320x240");
  if (imgsize == VC0706_160x120) Serial.println("160x120");

  Serial.println("Snap in 3 secs...");
  delay(3000);

  if (! cam.takePicture()) 
    Serial.println("Failed to snap!");
  else 
    Serial.println("Picture taken!");
  
  // Create an image with the name IMAGExx.JPG
  char filename[13];
  strcpy(filename, "IMAGE00.JPG");
  for (int i = 0; i < 100; i++) {
    filename[5] = '0' + i/10;
    filename[6] = '0' + i%10;
    // create if does not exist, do not open existing, write, sync after write
    if (! SD.exists(filename)) {
      break;
    }
  }
  
  // Open the file for writing
  File imgFile = SD.open(filename, FILE_WRITE);

  // Get the size of the image (frame) taken  
  uint16_t jpglen = cam.frameLength();
  Serial.print("Storing ");
  Serial.print(jpglen, DEC);
  Serial.print(" byte image.");

  int32_t time = millis();
  pinMode(8, OUTPUT);
  // Read all the data up to # bytes!
  byte wCount = 0; // For counting # of writes
  while (jpglen > 0) {
    // read 32 bytes at a time;
    uint8_t *buffer;
    uint8_t bytesToRead = min(32, jpglen); // change 32 to 64 for a speedup but may not work with all setups!
    buffer = cam.readPicture(bytesToRead);
    imgFile.write(buffer, bytesToRead);
    if(++wCount >= 64) { // Every 2K, give a little feedback so it doesn't appear locked up
      Serial.print('.');
      wCount = 0;
    }
    //Serial.print("Read ");  Serial.print(bytesToRead, DEC); Serial.println(" bytes");
    jpglen -= bytesToRead;
  }
  imgFile.close();

  time = millis() - time;
  Serial.println("done!");
  Serial.print(time); Serial.println(" ms elapsed");
}

void loop() {
 foto();
  delay(1000);
}

void foto(){
  Serial.println("VC0706 Camera snapshot test");
  
  // see if the card is present and can be initialized:
  if (!SD.begin(chipSelect)) {
    Serial.println("Card failed, or not present");
    // don't do anything more:
    return;
  }  
  
  // Try to locate the camera
  if (cam.begin()) {
    Serial.println("Camera Found:");
  } else {
    Serial.println("No camera found?");
    return;
  }
  // Print out the camera version information (optional)
  char *reply = cam.getVersion();
  if (reply == 0) {
    Serial.print("Failed to get version");
  } else {
    Serial.println("-----------------");
    Serial.print(reply);
    Serial.println("-----------------");
  }

  // Set the picture size - you can choose one of 640x480, 320x240 or 160x120 
  // Remember that bigger pictures take longer to transmit!
  
  //cam.setImageSize(VC0706_640x480);        // biggest
  cam.setImageSize(VC0706_320x240);        // medium
  //cam.setImageSize(VC0706_160x120);          // small

  // You can read the size back from the camera (optional, but maybe useful?)
  uint8_t imgsize = cam.getImageSize();
  Serial.print("Image size: ");
  if (imgsize == VC0706_640x480) Serial.println("640x480");
  if (imgsize == VC0706_320x240) Serial.println("320x240");
  if (imgsize == VC0706_160x120) Serial.println("160x120");

  Serial.println("Snap in 3 secs...");
  delay(3000);

  if (! cam.takePicture()) 
    Serial.println("Failed to snap!");
  else 
    Serial.println("Picture taken!");
  
  // Create an image with the name IMAGExx.JPG
  char filename[13];
  strcpy(filename, "IMAGE00.JPG");
  for (int i = 0; i < 100; i++) {
    filename[5] = '0' + i/10;
    filename[6] = '0' + i%10;
    // create if does not exist, do not open existing, write, sync after write
    if (! SD.exists(filename)) {
      break;
    }
  }
  
  // Open the file for writing
  File imgFile = SD.open(filename, FILE_WRITE);

  // Get the size of the image (frame) taken  
  uint16_t jpglen = cam.frameLength();
  Serial.print("Storing ");
  Serial.print(jpglen, DEC);
  Serial.print(" byte image.");

  int32_t time = millis();
  pinMode(8, OUTPUT);
  // Read all the data up to # bytes!
  byte wCount = 0; // For counting # of writes
  while (jpglen > 0) {
    // read 32 bytes at a time;
    uint8_t *buffer;
    uint8_t bytesToRead = min(32, jpglen); // change 32 to 64 for a speedup but may not work with all setups!
    buffer = cam.readPicture(bytesToRead);
    imgFile.write(buffer, bytesToRead);
    if(++wCount >= 64) { // Every 2K, give a little feedback so it doesn't appear locked up
      Serial.print('.');
      wCount = 0;
    }
    //Serial.print("Read ");  Serial.print(bytesToRead, DEC); Serial.println(" bytes");
    jpglen -= bytesToRead;
  }
  imgFile.close();

  time = millis() - time;
  Serial.println("done!");
  Serial.print(time); Serial.println(" ms elapsed");
  }

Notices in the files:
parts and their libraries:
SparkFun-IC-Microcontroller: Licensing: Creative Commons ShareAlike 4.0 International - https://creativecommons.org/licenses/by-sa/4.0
